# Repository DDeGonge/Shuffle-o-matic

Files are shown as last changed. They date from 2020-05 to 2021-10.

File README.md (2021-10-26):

# Shuffle-o-matic

Full overview video:
https://www.youtube.com/watch?v=eMTXyl7tPEk

Thingiverse page (cad files):
https://www.thingiverse.com/thing:4547302

## Significant experience recommended if you want to take on this project, it isn't documented very well :)

Hardware required
|Qty|Item|Supplier||
|---|---|---|---|
| | 3D printed Parts | |
| 3 | Nema 17 stepper motors, <=40mm long | [17HS15-1504S-X1 39mm long](https://www.aliexpress.com/item/1005002191787745.html?spm=2114.12010612.8148356.4.2bca2904n3VYBm)|
| 5 | Gates GT2 20t idlers with standoffs | |
| 3 | Gates GT2 20t drive pulleys | |
| 1 | MG90S servo | [MG90S servo](https://ebay.us/60Pxun) |
| 1 | 600rpm micro gearbox motor | [DC 3V 6V 12V GA12-N20](https://www.aliexpress.com/item/4000274747864.html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,searchweb201602_,searchweb201603_)|
| 2 | MGN9 linear profile bearings, 135mm len | [MGN9C](https://www.aliexpress.com/item/32773296501.html?spm=a2g0o.cart.0.0.54873c00SIeLte&mp=1) |
| 1 | MGN9 linear profile bearing, 95mm len | [MGN9C](https://www.aliexpress.com/item/32773296501.html?spm=a2g0o.cart.0.0.54873c00SIeLte&mp=1) |
| 6 | 6700 bearing | [6700ZZ](https://www.aliexpress.com/item/32852057465.html?spm=a2g0o.cart.0.0.54873c00SIeLte&mp=1) |
| 1 | Raspberry Pi | |
| 1 | (optional) Raspberry Pi Camera V1.4 | |
| 1 | (optional) 3x 3mm white led | |
| 1 | Adafruit Feather | |
| 1 | Breadboard/pcb for laying out components | |
| ~ | Assorted M2 and M3 nuts and bolts | |

All part numbers in the pcb should be accurate, though again review and order at your own risk. Use KiCad to view/edit, it's free!

And probably a few other things I'm forgetting. Seriously if you want to make this, do so at your own risk. Review the cad model yourself and make sure you have everything accounted for! This is not a project for beginners!

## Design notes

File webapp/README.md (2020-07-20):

Copy both of these files to /var/www/html/ on the Raspberry Pi to run on boot

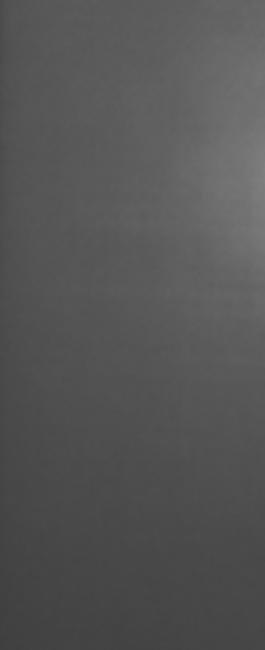
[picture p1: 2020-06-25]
helpers/Card_Imgs/cal.jpg

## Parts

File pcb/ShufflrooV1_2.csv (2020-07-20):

Id | Designator | Package | Quantity | Designation | Supplier and ref
1 | U1 | FeatherFootprint | 1 | FeatherM4
2 | J21,J9,J1,J8,J2,J4,J3,J14,J5,J6,J7 | PinHeader_1x02_P2.54mm_Vertical | 11 | Conn_01x02
3 | U2 | SOT-223 | 1 | AZ1117-3.3
4 | A3,A2,A1 | Pololu_Breakout-16_15.2x20.3mm | 3 | Pololu_Breakout_A4988
5 | J16 | PinHeader_1x08_P2.54mm_Vertical | 1 | Conn_01x08
6 | D2,D1 | LED_0603_1608Metric | 2 | LED
7 | R18 | R_0603_1608Metric | 1 | 1k5
8 | R17,R10 | R_0603_1608Metric | 2 | 174
9 | R16,R15,R14,R13,R12,R9,R8,R7,R6,R5,R4,R3,R2,R1,R19 | R_0603_1608Metric | 15 | 10k
10 | C2,C4,C1 | CP_Elec_6.3x5.8 | 3 | 47uF
11 | J15 | PinHeader_1x03_P2.54mm_Vertical | 1 | Conn_01x03
12 | J13 | BarrelJack_Wuerth_6941xx301002 | 1 | Conn_01x02
13 | Q1 | SOT-23 | 1 | PMV40UN2R
14 | R11 | R_0805_2012Metric | 1 | 1ohm
15 | J11,J12,J10 | PinSocket_1x04_P2.54mm_Vertical | 3 | Conn_01x04
16 | J17,J18,J19,J20 | MountingHole_2.7mm_M2.5_DIN965_Pad | 4 | Hole

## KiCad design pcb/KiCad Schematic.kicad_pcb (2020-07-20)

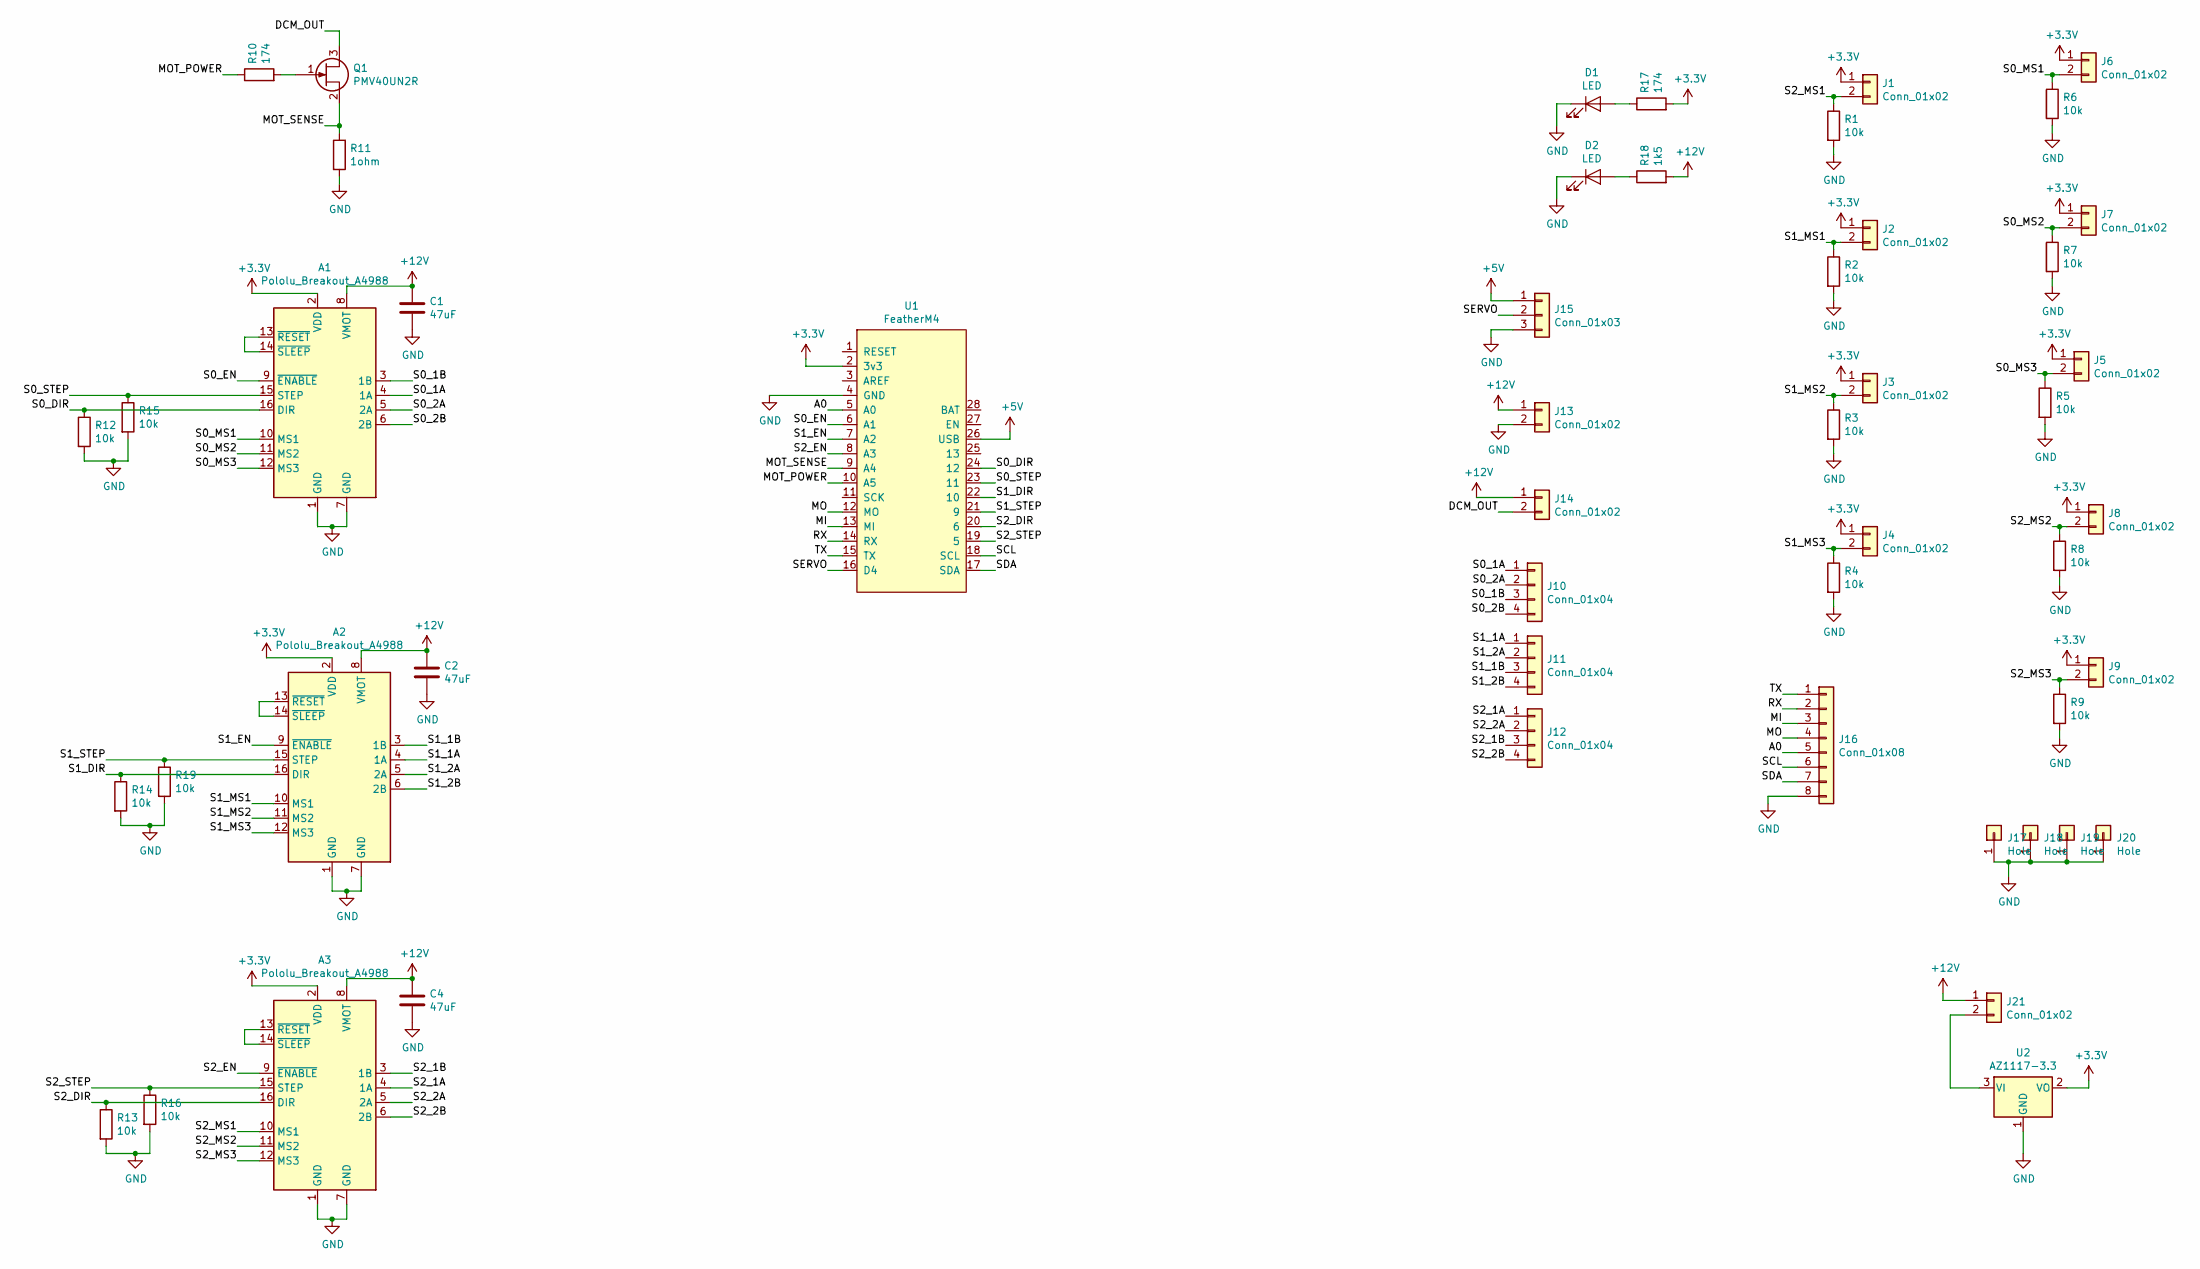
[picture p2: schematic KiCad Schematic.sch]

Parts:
A1, A2, A3: Pololu_Breakout_A4988; Pololu_Breakout-16_15.2x20.3mm
C1, C2, C4: 47uF; CP_Elec_6.3x5.8
D1, D2: LED; LED_0603_1608Metric
J1, J2, J3, J4, J5, J6, J7, J8, J9, J14, J21: Conn_01x02; PinHeader_1x02_P2.54mm_Vertical
J10, J11, J12: Conn_01x04; PinSocket_1x04_P2.54mm_Vertical
J13: Conn_01x02; BarrelJack_Wuerth_6941xx301002
J15: Conn_01x03; PinHeader_1x03_P2.54mm_Vertical
J16: Conn_01x08; PinHeader_1x08_P2.54mm_Vertical
J17, J18, J19, J20: Hole; MountingHole_2.7mm_M2.5_DIN965_Pad
Q1: PMV40UN2R; SOT-23
R1, R2, R3, R4, R5, R6, R7, R8, R9, R12, R13, R14, R15, R16, R19: 10k; R_0603_1608Metric
R10, R17: 174; R_0603_1608Metric
R11: 1ohm; R_0805_2012Metric
R18: 1k5; R_0603_1608Metric
U1: FeatherM4; FeatherFootprint
U2: AZ1117-3.3; SOT-223

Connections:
+3V3: A1.2 (VDD), A2.2 (VDD), A3.2 (VDD), J1.1, J2.1, J3.1, J4.1, J5.1, J6.1, J7.1, J8.1, J9.1, R17.2, U1.2 (3v3), U2.2 (VO)
+5V: J15.1, U1.26 (USB)
+12V: A1.8 (VMOT), A2.8 (VMOT), A3.8 (VMOT), C1.1, C2.1, C4.1, J13.1, J14.1, J21.1, R18.2
/A0: J16.5, U1.5 (A0)
/DCM_OUT: J14.2, Q1.3 (D)
/MI: J16.3, U1.13 (MI)
/MO: J16.4, U1.12 (MO)
/MOT_POWER: R10.1, U1.10 (A5)
/MOT_SENSE: Q1.2 (S), R11.1, U1.9 (A4)
/RX: J16.2, U1.14 (RX)
/S0_1A: A1.4 (1A), J10.1
/S0_1B: A1.3 (1B), J10.3
/S0_2A: A1.5 (2A), J10.2
/S0_2B: A1.6 (2B), J10.4
/S0_DIR: A1.16 (DIR), R12.1, U1.24 (12)
/S0_EN: A1.9 (~ENABLE), U1.6 (A1)
/S0_MS1: A1.10 (MS1), J6.2, R6.1
/S0_MS2: A1.11 (MS2), J7.2, R7.1
/S0_MS3: A1.12 (MS3), J5.2, R5.1
/S0_STEP: A1.15 (STEP), R15.1, U1.23 (11)
/S1_1A: A2.4 (1A), J11.1
/S1_1B: A2.3 (1B), J11.3
/S1_2A: A2.5 (2A), J11.2
/S1_2B: A2.6 (2B), J11.4
/S1_DIR: A2.16 (DIR), R14.1, U1.22 (10)
/S1_EN: A2.9 (~ENABLE), U1.7 (A2)
/S1_MS1: A2.10 (MS1), J2.2, R2.1
/S1_MS2: A2.11 (MS2), J3.2, R3.1
/S1_MS3: A2.12 (MS3), J4.2, R4.1
/S1_STEP: A2.15 (STEP), R19.1, U1.21 (9)
/S2_1A: A3.4 (1A), J12.1
/S2_1B: A3.3 (1B), J12.3
/S2_2A: A3.5 (2A), J12.2
/S2_2B: A3.6 (2B), J12.4
/S2_DIR: A3.16 (DIR), R13.1, U1.20 (6)
/S2_EN: A3.9 (~ENABLE), U1.8 (A3)
/S2_MS1: A3.10 (MS1), J1.2, R1.1
/S2_MS2: A3.11 (MS2), J8.2, R8.1
/S2_MS3: A3.12 (MS3), J9.2, R9.1
/S2_STEP: A3.15 (STEP), R16.1, U1.19 (5)
/SCL: J16.6, U1.18 (SCL)
/SDA: J16.7, U1.17 (SDA)
/SERVO: J15.2, U1.16 (D4)
/TX: J16.1, U1.15 (TX)
GND: A1.1 (GND), A1.7 (GND), A2.1 (GND), A2.7 (GND), A3.1 (GND), A3.7 (GND), C1.2, C2.2, C4.2, D1.1 (K), D2.1 (K), J13.2, J15.3, J16.8, J17.1, J18.1, J19.1, J20.1, R1.2, R2.2, R3.2, R4.2, R5.2, R6.2, R7.2, R8.2, R9.2, R11.2, R12.2, R13.2, R14.2, R15.2, R16.2, R19.2, U1.4 (GND), U2.1 (GND), U2.4
unnamed: A1.13 (~RESET), A1.14 (~SLEEP)
unnamed: A2.13 (~RESET), A2.14 (~SLEEP)
unnamed: A3.13 (~RESET), A3.14 (~SLEEP)
unnamed: D1.2 (A), R17.1
unnamed: D2.2 (A), R18.1
unnamed: J21.2, U2.3 (VI)
unnamed: Q1.1 (G), R10.2

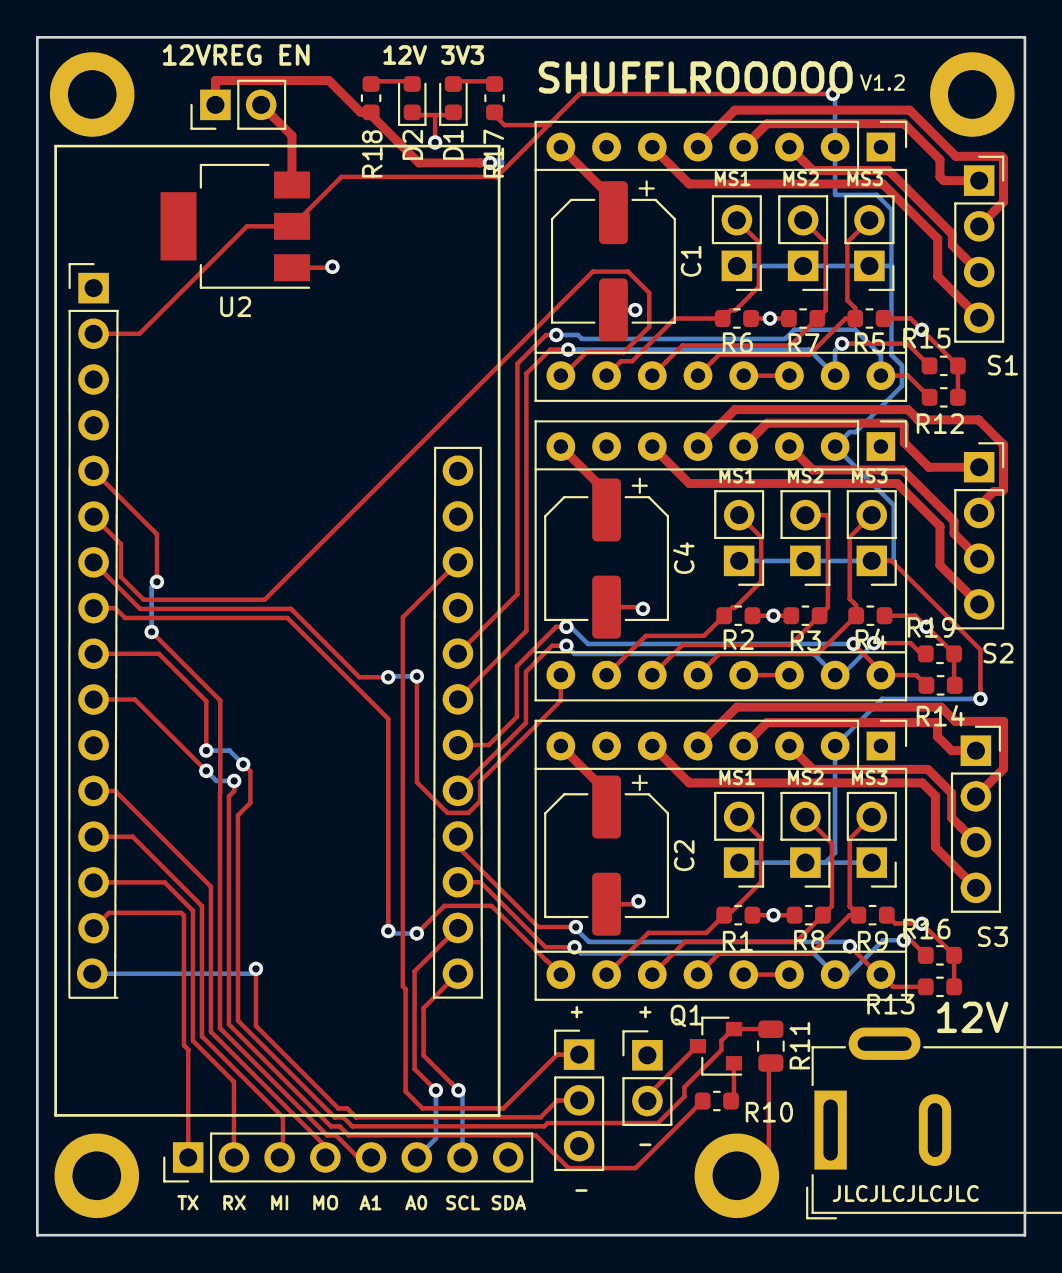
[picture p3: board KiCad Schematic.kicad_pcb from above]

Board: 2 copper layers, 54.9 x 66.5 mm, 51 parts (0 on the bottom side), 52 nets.

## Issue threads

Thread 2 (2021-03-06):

Use 150mm and 100mm linear rail

danobot, 2021-03-06:
Hey, just wondering if its possible to use 150mm and 100mm rails instead of the 135mm and 90mm ones as they are hard to find.

DDeGonge, 2021-03-08:
With some effort yes, you might have to make cuts in the external enclosure (they'll stick out a little) and/or slightly shift the hole pattern to get them to work properly.

danobot, 2021-03-08:
Thanks

Closed 2021-03-08.

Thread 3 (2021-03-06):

O-ring dimensions

danobot, 2021-03-06:
Hi, what size are the Orings you used?
Roller groves have a diameter of 13mm.

I found these clear silicone ones (food grade -  to avoid leaving black rubber marks on playing cards):
https://www.ebay.com.au/itm/White-Food-Grade-Silicone-O-Ring-O-Ring-10mm-50mm-OD-1mm-4mm-Wire-Diameter/133525117869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

They can be purchased with ID 13mm, 2mm thick and OD 15mm. The clearance for roller is 17.9mm

DDeGonge, 2021-03-08:
I'll try to find the bag tomorrow but I know they were a metric dash size and were a little under-sized so they would stretch and stay securely in place

Closed 2021-03-08.

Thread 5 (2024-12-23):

I'd appreciate a more detailed list of parts

Frits1980, 2024-12-23:
Hi,

First of: Thank you very very much for creating this. Exactly what I need.
But now I'm trying to find all parts, but have a hard time being sure I have the right part.
For instance:
- What are the dimensions of the idlers and the hole size? And what is standoff?
- Which Adafruit Feather do I need?

Also do I need the InventorCad files? Since I'm on a MAC I have no way of opening them.

Thank you in advance.

Kind regards,

Frits

Frits1980, 2025-03-04:
@danobot could you help me with this? Pretty please :)

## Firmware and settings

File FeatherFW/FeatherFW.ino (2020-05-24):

#include "shuffler.h"

#define Serial SERIAL_PORT_USBVIRTUAL

void setup() 
{ 
  pinMode(dcmotor_power, OUTPUT);
  pinMode(dcmotor_sense, INPUT);

  Serial.begin(250000);
  pixel.begin();
  disp_servo.attach(servo_pin);
  disp_servo.write(135);
  delay(500);
  disp_servo.detach();
}

void loop() 
{
  // Initialize some stuff
  setLEDColor(200,0,0);
  unsigned long startTime_us = micros();
  unsigned long t_elapsed_us;
  stepper_obj s0, s1, s2;
  stepper_obj all_steppers[3] = {s0, s1, s2};
  all_steppers[0].init(s0_step, s0_dir, s0_en, true);
  all_steppers[1].init(s1_step, s1_dir, s1_en, true);
  all_steppers[2].init(s2_step, s2_dir, s2_en, false);
  global_config settings;
  
  char serial_data[100];
  setLEDColor(100,0,0);

  // Start main response loop
  while(true)
  {
    t_elapsed_us = micros() - startTime_us;
    clear_data(serial_data);
    if(respondToSerial(serial_data)){
      setLEDColor(100,50,0);
      switch (serial_data[0]){
        case 'm':{
          // Move stepper motors
          // m,S_INDEX,S_TARPOS,S_VEL,S_ACCEL
          vector<int32_t> args;
          parse_inputs(serial_data, args);
          all_steppers[args[0]].move_motor(args[1], args[2], args[3]);
          break;
        }
        case 's':{
          // Enable stepper index
          int s_index = (int)serial_data[2] - '0';
          all_steppers[s_index].enable();
          break;
        }
        case 'x':{
          // Disable stepper index
          int s_index = (int)serial_data[2] - '0';
          all_steppers[s_index].disable();
          break;
        }
        case 'z':{
          // Set stepper positions or zero
          // z,S_INDEX,S_TARGET
          vector<int32_t> args;
          parse_inputs(serial_data, args);
          all_steppers[args[0]].overwrite_pos(args[1]);
          break;
        }
        case 'h':{
          // Home steppers
          break;
        }
        case 'e':{
          // Enable dispense motor
          digitalWrite(dcmotor_power, HIGH);
          disp_servo.attach(servo_pin);
          break;
        }
        case 'd':{
          // Disable dispense motor
          digitalWrite(dcmotor_power, LOW);
          disp_servo.detach();
          break;
        }
        case 'c':{
          // Dispense one card, with verification
          bool resp = dispense_card(settings);
          if(!resp){
            Serial.println("JAM");
          }
          break;
        }
        case 'b':{
          // Baseline dispense motor current
          cur_baseline = calc_cur_threshold(1000);
          Serial.println(cur_baseline);
          break;
        }
        case 'p':{
          // Get all stepper positions
          Serial.print('p');
          for(uint8_t j = 0; j < 3; j++){
            Serial.print(',');
            Serial.print(all_steppers[j].get_pos());
          }
          Serial.println();
          break;
        }
        case 'f':{
          // Configure stepper object
          // f,S_INDEX,STEPSPERMM*1000
          vector<int32_t> args;
          parse_inputs(serial_data, args);
          all_steppers[args[0]].update_config(args[1]);
          break;
        }
        case 'g':{
          // Configure global setting
          // g,SETTING_CHAR,NEWVALUE
          vector<int32_t> args;
          parse_inputs(serial_data, args);
          update_settings(settings, args);
        }
      }
      Serial.println("ok");
      setLEDColor(0,100,0);
    }
  }
  while(true);
}

void update_settings(global_config &settings, vector<int32_t> args){
  switch(args[0]){
    case 49:{  // a
      settings.step_len_us = args[1];
      break;
    }
    case 50:{  // b
      settings.servo_min_pwm = args[1];
      break;
    }
    case 51:{  // c
      settings.servo_max_pwm = args[1];
      break;
    }
    case 52:{  // d
      settings.dispense_timeout_ms = args[1];
      break;
    }
    case 53:{  // e
      settings.current_detect_freq_hz = args[1];
      break;
    }
    case 54:{  // f
      settings.current_detect_window_ms = args[1];
      break;
    }
    case 55:{  // g
      float new_val = float(args[1]) / 1000;
      settings.current_threshold_factor = new_val;
      break;
    }
    case 56:{  // h
      settings.servo_return_time_ms = args[1];
      break;
    }
    case 57:{  // i
      settings.dispense_max_attempts = args[1];
      break;
    }
  }
}

float calc_cur_threshold(uint16_t n_samples){
  float sum = 0;
  delay(200);
  for(uint16_t i = 0; i < n_samples; i++){
    sum += analogRead(dcmotor_sense);
    delay(1);
  }
  return (sum / n_samples);
}

bool dispense_card(global_config settings){
  uint32_t cur_window_len = settings.current_detect_freq_hz * settings.current_detect_window_ms;
  cur_window_len /= 1000;
  uint16_t cur_window[cur_window_len];
  uint32_t dwell_time_us = 1000000 / settings.current_detect_freq_hz;
  float window_mean = 0;
  uint16_t window_i = 0;
  for(uint8_t i = 0; i < cur_window_len; i++){cur_window[i] = 0;}

  bool disp_success = false;
  for(uint8_t i = 0; i < settings.dispense_max_attempts; i++){
    disp_servo.write(settings.servo_min_pwm);
  
    // Wait until card is detected from dispense motor current spike
    uint32_t t_start_ms = millis();
    while(millis() < (t_start_ms + settings.dispense_timeout_ms)){
      cur_window[window_i] = analogRead(dcmotor_sense);
      window_i++;
      window_i %= cur_window_len;
      window_mean = calc_mean(cur_window);
      if(window_mean >= (cur_baseline * settings.current_threshold_factor)){
        disp_success = true;
        break;
      }
      delayMicroseconds(dwell_time_us);
    }

    disp_servo.write(settings.servo_max_pwm);

    if(disp_success==true){
      break;
    }

    delay(settings.servo_return_time_ms);
  }

  // check for jam
  if(calc_cur_threshold(100) > (cur_baseline * 2 * settings.current_threshold_factor)){
    return false;
  }
  return disp_success;
}

float calc_mean(uint16_t window[]){
  float sum = 0;
  for(uint16_t i = 0; i < cur_window_len; i++){
    sum += window[i];
  }
  return (sum / cur_window_len);
}

void parse_inputs(char serial_data[100], vector<int32_t> &args){
  char delim = ',';
  uint32_t index = 0;
  vector<char> temp_arg_char;

  // Gets past command char to first data
  while(serial_data[index] != delim){index++;}
  index++;
  while(serial_data[index] != '\0'){
    temp_arg_char.push_back(serial_data[index]);
    index++;
    if(serial_data[index] == delim){
      args.push_back(vtoi(temp_arg_char));
      temp_arg_char.clear();
      index++;
    }
  }
  args.push_back(vtoi(temp_arg_char));
}

int32_t vtoi(vector<char> vec)
{
  int32_t ret = 0;
  int mult = pow(10 , (vec.size()-1));

  for(int i = 0; i <= vec.size(); i++) {
    ret += (vec[i] - '0') * mult;
    mult /= 10;
  }
  return ret;
}

// Read serial messages if exist
bool respondToSerial(char (&serial_data) [100])
{
  uint8_t index = 0;
  if (Serial.available() > 0){
    while (Serial.available() > 0) {
      char newchar = Serial.read();
      if(newchar != '\n'){
        serial_data[index] = newchar;
        index++;
      }
      else{
        break;
      }
    }
    return true;
  }
  return false;
}

void clear_data(char (&serial_data) [100]){
  for(uint16_t i = 0; i < 100; i++){
    serial_data[i]='\0';
    }
}

void setLEDColor(int r, int g, int b)
{
  pixel.setPixelColor(0, pixel.Color(r,g,b)); // Set LED to red
  pixel.show();
}

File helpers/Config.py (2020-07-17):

""" MOTOR PARAMETERS """
b_step_per_mm = 80
d_step_per_mm = 80
p_step_per_mm = 80

step_len_us = 1  # NOT CURRENTLY USED

disp_move_mm = 104
disp_vel_mmps = 50
disp_acc_mmps2 = 100

pusher_move_mm = 68
pusher_vel_mmps = 520
pusher_acc_mmps2 = 12500

bin_vel_mmps = 400
bin_acc_mmps2 = 3500

bin_heights_load_mm = [2.5, 10.2, 17.9, 25.6, 33.3, 41.0, 48.7, 56.4]  # bin 0 (bottom) to bin n (top)
bin_unload_shift_mm = 30


""" DISPENSE PARAMETERS """
dc_motor_spin_down_dwell_s = 0.4
min_time_between_dispenses_s = 0.3
servo_min_pwm = 25
servo_max_pwm = 160
dispense_timeout_ms = 600
current_detect_freq_hz = 500
current_detect_window_ms = 100
current_threshold_factor = 1500  # Multiply by 1000, must be int
servo_return_time_ms = 500
dispense_max_attempts = 3


""" SHUFFLING PARAMETERS """
cards_per_shuffle_loop = 20  # Too many and it may fail to dispense
shuffle_loops = 4
max_cards_per_bin = 10
planned_shuffle_timeout = 150 # If this many cards were trashed and deck still isn't in order, give up


""" CAMERA PARAMETERS """
# Cropped region of card window
H_MIN = 75
H_MAX = 700
W_MIN = 550
W_MAX = 775
IMAGE_RESOLUTION = (1920,1080)
IMAGE_ROTATION_DEGS = 0


""" DETECTION PARAMETERS """
RANK_DIFF_MAX = 2000
SUIT_DIFF_MAX = 1000
RANK_WIDTH = 70
RANK_HEIGHT = 125
SUIT_WIDTH = 70
SUIT_HEIGHT = 100
MAX_CONTOURS_TO_CHECK = 5

USE_CAL_IMAGE = True
BW_THRESH = 15


""" FEATHER COMM PARAMETERS """
# Chars used for setting parameters on feather. All vars here must be int
Feather_Parameter_Chars = {
    'a': step_len_us,
    'b': servo_min_pwm,
    'c': servo_max_pwm,
    'd': dispense_timeout_ms,
    'e': current_detect_freq_hz,
    'f': current_detect_window_ms,
    'g': current_threshold_factor,
    'h': servo_return_time_ms,
    'i': dispense_max_attempts
}

""" DEBUG PARAMS """
DEBUG_MODE = False

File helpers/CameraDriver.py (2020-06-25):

__version__ = '0.1.0'

import sys
import time
import os
import cv2
import scipy.misc
import helpers.Config as cfg
import numpy as np

from picamera.array import PiRGBArray
from picamera import PiCamera
from PIL import Image

from helpers.Gameplay import ALLRANKS, ALLSUITS, Card


class Train_Obj(object):
    """ Stores training image and name for either rank or suit set """
    def __init__(self, img = [], name = None):
        self.img = img
        self.name = name

class Camera(object):
    TRAIN_PATH = 'helpers/Card_Imgs'
    def __init__(self, resolution=cfg.IMAGE_RESOLUTION):
        self.camera = None
        self.resolution = resolution
        self.train_ranks = self.load_calibration_set(self.TRAIN_PATH, ALLRANKS)
        self.train_suits = self.load_calibration_set(self.TRAIN_PATH, ALLSUITS)
        self.white_offset_img = self.load_offset_image(self.TRAIN_PATH, 'cal.jpg')

    def read_card(self, enable_and_disable: bool = False):
        image = self._capture_image(enable_and_disable)
        processed_img = self.preprocess_image(image)
        return self.match_card(processed_img)

    def exposure_sweep(self, exposures):
        img = self._capture_image(enable_and_disable=True)
        return [self.preprocess_image(img, int(exp)) for exp in exposures]

    def _capture_image(self, enable_and_disable):
        if enable_and_disable:
            self.start_camera()
        rawCapture = PiRGBArray(self.camera)
        self.camera.capture(rawCapture, format="bgr")
        if enable_and_disable:
            self.stop_camera()
        return rawCapture.array

    @staticmethod
    def _display_image(img):
        cv2.imshow("Image", img)
        cv2.waitKey(0)

    @staticmethod
    def _save_image(img, path):
        scipy.misc.toimage(img, cmin=0.0, cmax=...).save('path')

    def start_camera(self):
        self.camera = PiCamera()
        self.configure_camera()

    def configure_camera(self):
        self.camera.rotation = cfg.IMAGE_ROTATION_DEGS
        self.camera.resolution = self.resolution
        self.camera.exposure_mode = 'off'

    def stop_camera(self):
        self.camera.close()

    """ Image recognition functions """

    def preprocess_image(self, img, exp_threshold = None):
        gray = cv2.cvtColor(img,cv2.COLOR_BGR2GRAY)
        blur = cv2.GaussianBlur(gray,(5,5),0)
        blur_crop = blur[cfg.H_MIN:cfg.H_MAX, cfg.W_MIN:cfg.W_MAX]
        if cfg.USE_CAL_IMAGE:
            # Subtract from background white cal image before thresholding
            blur_crop = self.white_offset_img - blur_crop
            blur_crop[blur_crop > 200] = 0
            if cfg.DEBUG_MODE:
                debug_save_img(blur_crop, 'offset_greyscale.jpg')
                debug_save_img(blur, 'greyscale.jpg')
            
        if exp_threshold is None:
            exp_threshold = cfg.BW_THRESH
        _, proc_img = cv2.threshold(blur_crop, exp_threshold, 255, cv2.THRESH_BINARY)

        if not cfg.USE_CAL_IMAGE:
            proc_img = cv2.bitwise_not(processed_image)

        if cfg.DEBUG_MODE:
            debug_save_img(proc_img, 'thresholded.jpg')

        return proc_img

    def match_card(self, processed_image):
        """ Finds best rank and suit matches for the query card. Differences
        the query card rank and suit images with the train rank and suit images.
        The best match is the rank or suit image that has the least difference."""

        qCard = Card()

        # Invert image and find contours
        _, contours, _ = cv2.findContours(processed_image, cv2.RETR_TREE,cv2.CHAIN_APPROX_SIMPLE)
        contours = sorted(contours, key=cv2.contourArea, reverse=True)

        # Trim smallest contours if too many found
        if len(contours) > cfg.MAX_CONTOURS_TO_CHECK:
            contours = contours[:cfg.MAX_CONTOURS_TO_CHECK]

        # Crop contour regions and save as image array to card
        def contour_to_bb(contour):
            x,y,w,h = cv2.boundingRect(contour)
            return processed_image[y:y+h, x:x+w]
        qCard.test_imgs = [contour_to_bb(contour) for contour in contours]

        best_rank_match_diff = 10000
        best_suit_match_diff = 10000

        # Must find at least 2 to find both rank and suit
        if len(qCard.test_imgs) < 2:
            return qCard

        for i, test_img in enumerate(qCard.test_imgs):
            # Find best rank match
            rank_img = cv2.resize(test_img, (cfg.RANK_WIDTH, cfg.RANK_HEIGHT), interpolation=cv2.INTER_CUBIC)
            for Trank in self.train_ranks:
                diff_img = cv2.absdiff(rank_img, Trank.img)
                rank_diff = int(np.sum(diff_img)/255)
                
                if rank_diff < min(best_rank_match_diff, cfg.RANK_DIFF_MAX):
                    best_rank_match_diff = rank_diff
                    qCard.rank = Trank.name

            # Same process with suit images
            suit_img = cv2.resize(test_img, (cfg.SUIT_WIDTH, cfg.SUIT_HEIGHT), interpolation=cv2.INTER_CUBIC)
            for Tsuit in self.train_suits:
                diff_img = cv2.absdiff(suit_img, Tsuit.img)
                suit_diff = int(np.sum(diff_img)/255)
                
                if suit_diff < min(best_suit_match_diff, cfg.SUIT_DIFF_MAX):
                    best_suit_match_diff = suit_diff
                    qCard.suit = Tsuit.name

            if cfg.DEBUG_MODE:
                print('rank:', qCard.rank, best_rank_match_diff)
                print('suit:', qCard.suit, best_suit_match_diff)
                debug_save_img(rank_img, 'rank{}.jpg'.format(i))
                debug_save_img(suit_img, 'suit{}.jpg'.format(i))

            if i >= 2 and qCard.rank is not None and qCard.suit is not None:
                break

        return qCard

    @staticmethod
    def load_calibration_set(filepath, set_names):
        """ Loads calibration rank or suit images to create calibration set. """
        def gen_obj(i):
            img = cv2.imread(os.path.join(filepath, i + '.jpg'), cv2.IMREAD_GRAYSCALE)
            return Train_Obj(img=img, name=i)

        return [gen_obj(i) for i in set_names]

    @staticmethod
    def load_offset_image(filepath, filename):
        import_img = cv2.imread(os.path.join(filepath, filename))
        return cv2.cvtColor(import_img,cv2.COLOR_BGR2GRAY)


if __name__=='__main__':
    c = Camera()
    card = c.read_card(enable_and_disable=True)
    print(card.rank, card.suit)


def debug_save_img(img, imgname):
    im = Image.fromarray(img)
    im.save(os.path.join('/home/pi/', imgname))

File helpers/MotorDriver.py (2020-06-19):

__version__ = '0.1.0'

import helpers.Config as cfg
import time
import math

DEBUG = True

class Motor:
    def __init__(self, serial_device, stepspermm, stepper_index):
        self.steps_per_mm = stepspermm
        self.serial_device = serial_device
        self.stepper_index = stepper_index
        self.error = 0.
        self.configure()

    def home(self):
        self.relative_move(-300)
        if self.is_homed:
        	self.relative_move(3)
        	self.relative_move(-5,1,50)
        if not self.is_homed:
        	raise('Error: Failed to home')
        print('homed')

    def zero(self):
        self.serial_device.command('z,' + str(self.stepper_index) + ',0')

    def enable(self):
        self.serial_device.command('s,' + str(self.stepper_index))

    def disable(self):
        self.serial_device.command('x,' + str(self.stepper_index))

    def update_defaults(self, vel, acc):
        self.def_vel = vel
        self.def_acc = acc

    def configure(self, steps_per_mm=None):
        if not steps_per_mm:
            steps_per_mm = self.steps_per_mm

        self.serial_device.command('f,' + str(self.stepper_index) + ',' + str(1000 * steps_per_mm))

    def absolute_move(self, distance_mm, velocity_mmps=None, accel_mmps2=None):
        # Pull defaults if vel or acc not specified
        if velocity_mmps is None:
            velocity_mmps = self.def_vel
        if accel_mmps2 is None:
            accel_mmps2 = self.def_acc

        # Calculate move
        command = 'm,' + str(self.stepper_index) + ',' + str(self._calc_steps(distance_mm)) + ',' + str(velocity_mmps) + ',' + str(accel_mmps2)
        self.serial_device.command(command)

    def relative_move(self, distance_mm, velocity_mmps=None, accel_mmps2=None):
         return self.absolute_move(self.pos_mm + distance_mm, velocity_mmps, accel_mmps2)

    @property
    def is_homed(self):
        return True

    @property
    def pos_mm(self):
        resp = self.serial_device.command('p').strip('\n').split(',')
        return int(resp[self.stepper_index + 1]) / self.steps_per_mm

    def _calc_steps(self, dist_mm):
        steps_tot = (dist_mm + self.error) * self.steps_per_mm
        steps = math.floor(steps_tot)
        self.error = steps_tot - steps
        return steps

class DispenseStep(Motor):
    def __init__(self, **kwargs):
        super().__init__(**kwargs, stepspermm = cfg.d_step_per_mm, stepper_index = 2)
        self.update_defaults(cfg.disp_vel_mmps, cfg.disp_acc_mmps2)

    def raise_stage(self):
        self.absolute_move(cfg.disp_move_mm, cfg.disp_vel_mmps, cfg.disp_acc_mmps2)

    def lower_stage(self):
        self.absolute_move(0.2, cfg.disp_vel_mmps, cfg.disp_acc_mmps2)


class PushStep(Motor):
    def __init__(self, **kwargs):
        super().__init__(**kwargs, stepspermm = cfg.p_step_per_mm, stepper_index = 1)
        self.update_defaults(cfg.pusher_vel_mmps, cfg.pusher_acc_mmps2)

    def run(self, dwell_s=0.1):
        self.absolute_move(cfg.pusher_move_mm, cfg.pusher_vel_mmps, cfg.pusher_acc_mmps2)
        time.sleep(dwell_s)
        self.absolute_move(0.2, cfg.pusher_vel_mmps, cfg.pusher_acc_mmps2)


class BinStep(Motor):
    def __init__(self, **kwargs):
        super().__init__(**kwargs, stepspermm = cfg.b_step_per_mm, stepper_index = 0)
        self.update_defaults(cfg.bin_vel_mmps, cfg.bin_acc_mmps2)

    def load_bin_pos(self, bin_num):
        self.absolute_move(cfg.bin_heights_load_mm[bin_num], cfg.bin_vel_mmps, cfg.bin_acc_mmps2)

    def unload_bin_pos(self, bin_num):
        self.absolute_move(cfg.bin_heights_load_mm[bin_num] + cfg.bin_unload_shift_mm, cfg.bin_vel_mmps, cfg.bin_acc_mmps2)

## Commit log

2019-09-03 motor routines and stuff
2019-09-05 update pin, fix function error
    [Config.py]
2019-10-28 rework motor driver
2019-10-28 reorder driver list
2019-10-28 change motor driver to use rpi.gpio
2019-10-28 limit switch and homing support
2019-10-28 remove auto home for motors
2019-11-03 add servo driver features
2019-11-09 driver updates
2019-11-09 servo driver update
2019-11-09 add servo destructor
2019-11-09 improve servo control
2019-11-09 add slow servo move
2019-11-09 temp disable camera driver
2019-11-09 test servo dispense
2019-11-09 improve servo dispense routine
2020-01-05 add dc motor driver support, single direction
2020-01-05 enable dispense motor control in loop
2020-01-07 bugfix dcmotor driver
2020-04-06 convert code to use feather aux board for low level control
2020-04-19 camera stuff plus debugging
2020-04-19 attempt to bugfix camera
2020-04-19 stupid filepath bug fix
    [CameraDriver.py]
2020-04-19 repeated measurements and add error report
    [ShuffleScript.py]
2020-04-19 even more debuggin prints
2020-04-19 maybe this will fix contours
    [Config.py]
2020-05-07 big changes for soldered pcb version
2020-05-24 working with custom pcb, add a bunch of features and improve speed and reliability
2020-06-17 bugfixes and progress - needs some refactoring
    [ShuffleScript.py, WebFuncs.py]
2020-06-18 camera tweaks
2020-06-18 cfg updates and cal img name fixes
    [Config.py]
2020-06-19 add exposure calibration help function
2020-06-19 camera stuff
2020-06-21 camera bugfixes
2020-06-21 bugfixes, working with blackjack now
    [CameraDriver.py, Config.py, Gameplay.py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]
2020-06-24 update config and pinout for pcb v1.2
2020-06-25 only read card once and first try auto calibration
2020-06-25 add greyscale calibration offset
2020-06-25 update cam filtering
2020-07-01 update to use dispenser stepper
2020-07-01 config update and minor bugfix
    [Config.py, ShuffleScript.py]
2020-07-06 update calibration images
2020-07-20 add pcb files
    [KiCad Schematic-B.Cu.gbl, KiCad Schematic-B.Mask.gbs, KiCad Schematic-Edge.Cuts.gm1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]
2021-03-06 docs: bom
2021-03-06 docs: fix Nema link to be for a product <= 40mm
2021-06-30 add main assembly step file
